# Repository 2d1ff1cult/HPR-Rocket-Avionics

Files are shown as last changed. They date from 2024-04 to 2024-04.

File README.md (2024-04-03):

# HPR Rocket Avionics
Code for data acquisition electronics on a Tripoli Level 1 High Power Rocket (HPR)

Model as of 4/2/2024:
As of 4/2/2024, this is the first iteration. Currently just collects data and ~~stores on SD card~~ displays to ground station serial monitor.
Uses nRF24L01+ 2.4GHz modules for radio communication.

Features the uses of remove before flight (RBF) tags connected to SPDT switches in a custom CAD assembly to actuate GPS and logging first, then the Arduino Nano.
handdrawn schematic

Why? GPS cold starts are a big issue; starting the GPS at least 15 minutes before the entire data logging circuit allows for satellite acquisition as you drive to rocket launch destination.

Sample data looks like this:
sampledata

Second iteration will be an upgrade to 900MHz with RYLR998 and data logging. Possibly even control loops for fin actuation.

Future goals involve creating an OSD visualization of the data (which are altitude, air pressure, speed, XYZ accel, and GPS) similar to SpaceX launches. This is what inspired this work


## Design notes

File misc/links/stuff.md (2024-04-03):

arduino
https://support.arduino.cc/hc/en-us/articles/4841602539164-Burn-the-bootloader-on-UNO-Mega-and-classic-Nano-using-another-Arduino

nrf24l01
https://lastminuteengineers.com/nrf24l01-arduino-wireless-communication/
https://forum.arduino.cc/t/simple-nrf24l01-2-4ghz-transceiver-demo/405123/2

gps
https://github.com/SlashDevin/NeoGPS/blob/master/examples/NMEASDlog/NMEASDlog.ino

lora
https://how2electronics.com/reyax-rylr890-lora-module-with-arduino/
https://www.thethingsnetwork.org/docs/lorawan/spreading-factors/
https://www.youtube.com/watch?v=dxYY097QNs0
https://www.youtube.com/watch?v=B580NvdXtjs

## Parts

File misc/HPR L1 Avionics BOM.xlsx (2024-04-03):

Quantity | Component | Dimensions | Links | Notes
2 | Microcontroller Unit (MCU): Arduino Nano | 45mm x 18mm | link (https://www.ebay.com/itm/364546971433?itmmeta=01HTH1EPV5RG68D9N0ZWATMX4W) | Need CH340 drivers
1 | Accelerometer + Gyroscope + Compass: MPU9250 | 15mm x 25mm | link (https://www.ebay.com/itm/404781821679?itmmeta=01HTH1E781Y8EGJHDQG15KYYSF)
2 | 900MHz Long Range Radio (LoRa): RYLR998 | 32mm x 14mm | link (https://www.amazon.com/gp/product/B099RM1XMG/ref=ppx_yo_dt_b_search_asin_title?ie=UTF8&psc=1)
1 | Altimeter: BMP388 | 169mm x 66mm | link (https://www.amazon.com/gp/product/B09FG4NXFJ/ref=ppx_yo_dt_b_search_asin_title?ie=UTF8&psc=1)
1 | GPS: NEO-6M | 90mm x 55mm | link (https://www.amazon.com/gp/product/B0CPX7B1KW/ref=ppx_yo_dt_b_search_asin_title?ie=UTF8&psc=1)
1 | SD Reader: HW125 SD Reader Breakout Board | 102mm x 79mm | link (https://www.amazon.com/gp/product/B07BJ2P6X6/ref=ppx_yo_dt_b_search_asin_title?ie=UTF8&psc=1)
2 | buck regulators | 20mm x 11mm | link (https://www.amazon.com/gp/product/B08R6337QY/ref=ppx_yo_dt_b_search_asin_title?ie=UTF8&psc=1)
2 | SPDT switches | 20mm x 10mm | link (https://www.amazon.com/gp/product/B07MW2RPJY/ref=ppx_yo_dt_b_search_asin_title?ie=UTF8&psc=1) | for use with RBF switches

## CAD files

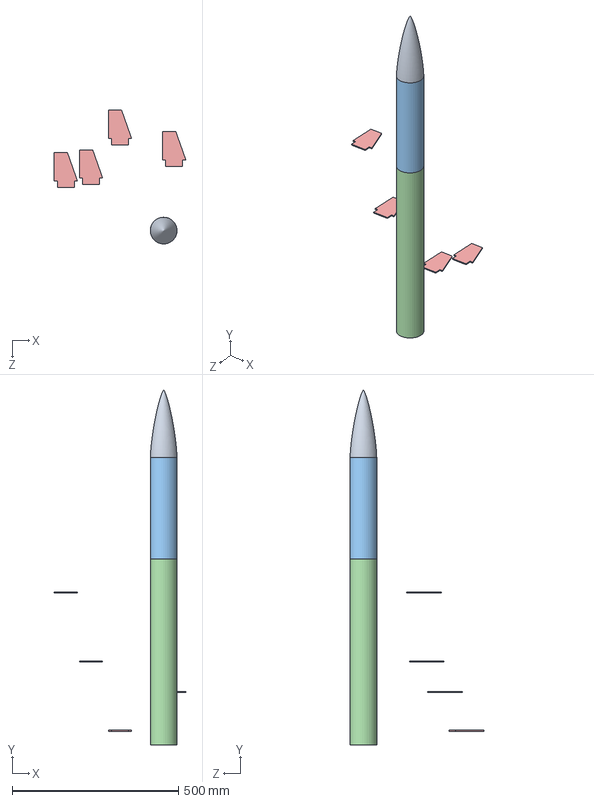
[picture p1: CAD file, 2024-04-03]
cad/Jerome_Rocket.SLDASM
395.8 x 1066.8 x 402.4 mm
Jerome Bulkhead
Jerome Fins x 4
Jerome Lower Body Tube
Jerome Top Body Tube
Jerome Tube Coupler
Jerome_Nose_Cone

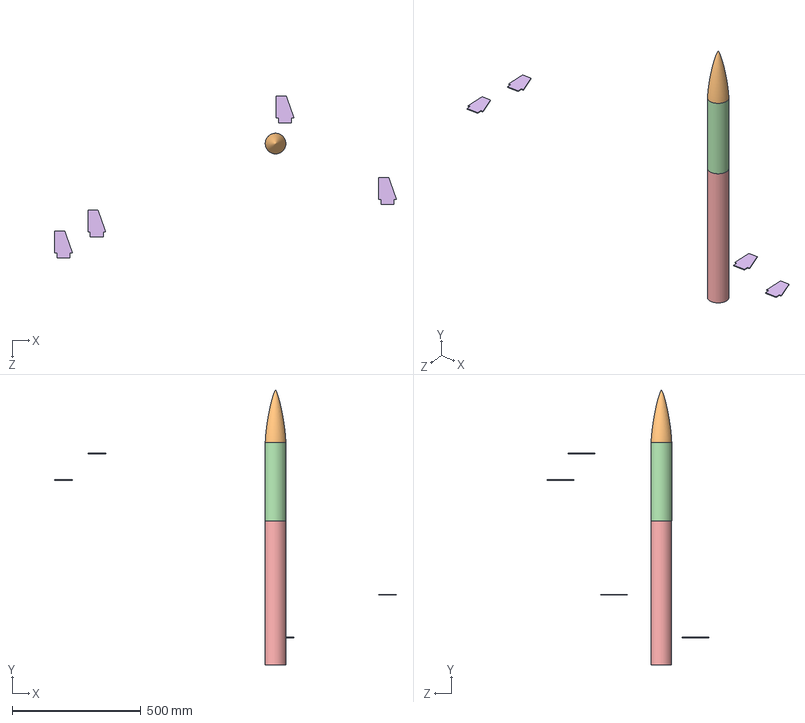
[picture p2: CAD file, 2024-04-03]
cad/Jerome_Rocket rev2.SLDASM
1326.9 x 1066.8 x 627.6 mm
Jerome Bulkhead
Jerome Centering Ring x 3
Jerome Fins x 4
Jerome Lower Body Tube
Jerome Top Body Tube
Jerome Tube Coupler
Jerome_Nose_Cone
Jerome Inner Tube

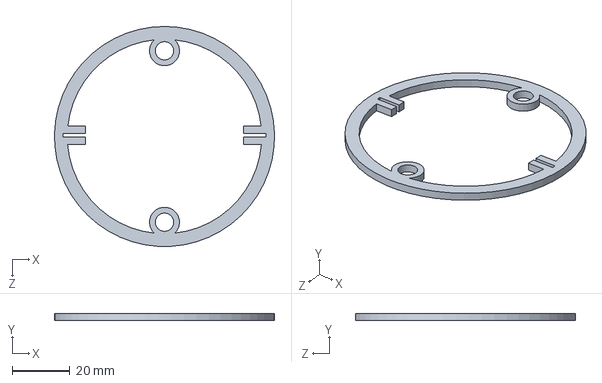
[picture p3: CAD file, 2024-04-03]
cad/PCB_coupler_crosssection.SLDPRT
76.2 x 2.54 x 76.2 mm

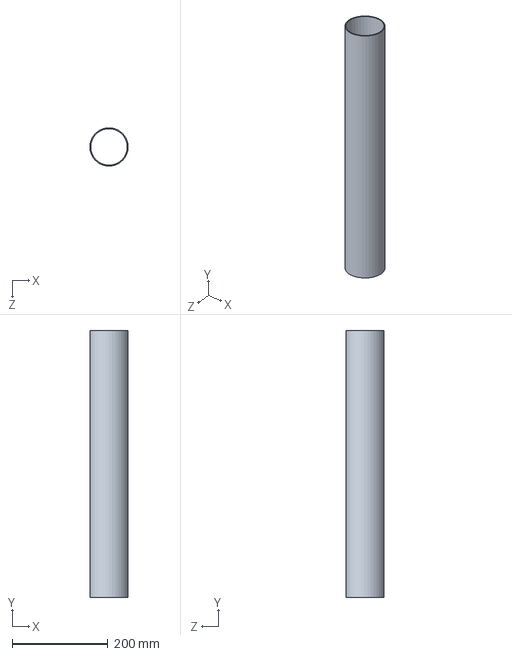
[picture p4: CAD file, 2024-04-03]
cad/Jerome Lower Body Tube.SLDPRT
80.2 x 558.8 x 80.2 mm

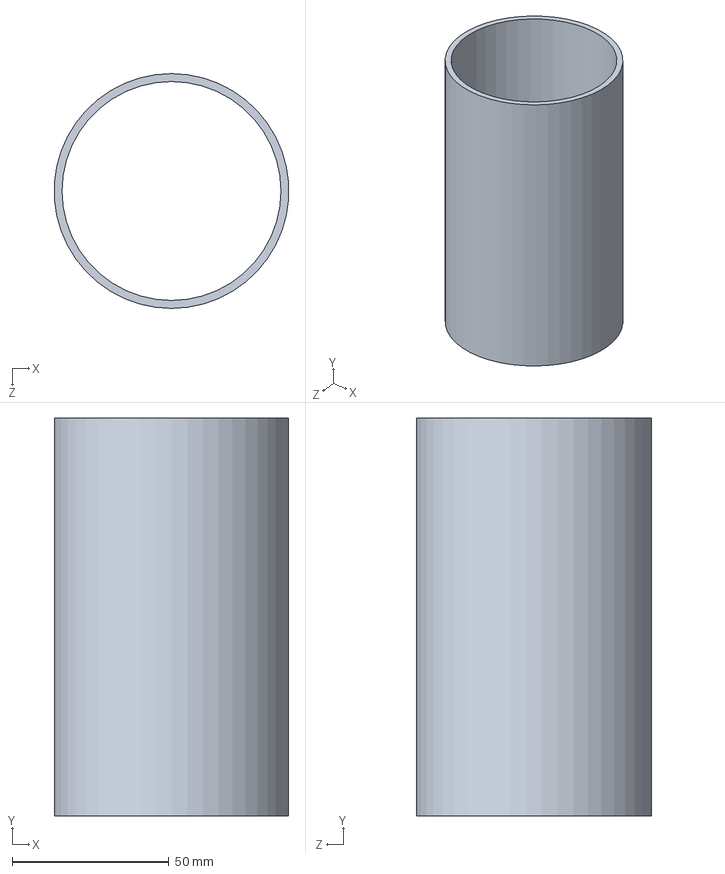
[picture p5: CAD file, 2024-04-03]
cad/Jerome Tube Coupler.SLDPRT
74.8 x 127.0 x 74.9 mm

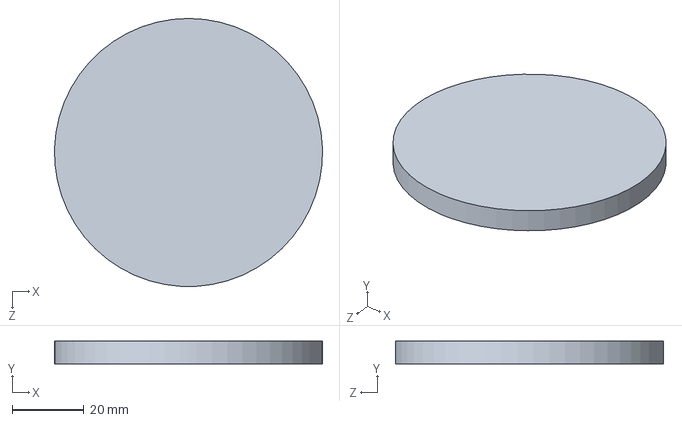
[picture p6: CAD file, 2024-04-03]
cad/Jerome Bulkhead.SLDPRT
74.9 x 6.35 x 74.9 mm

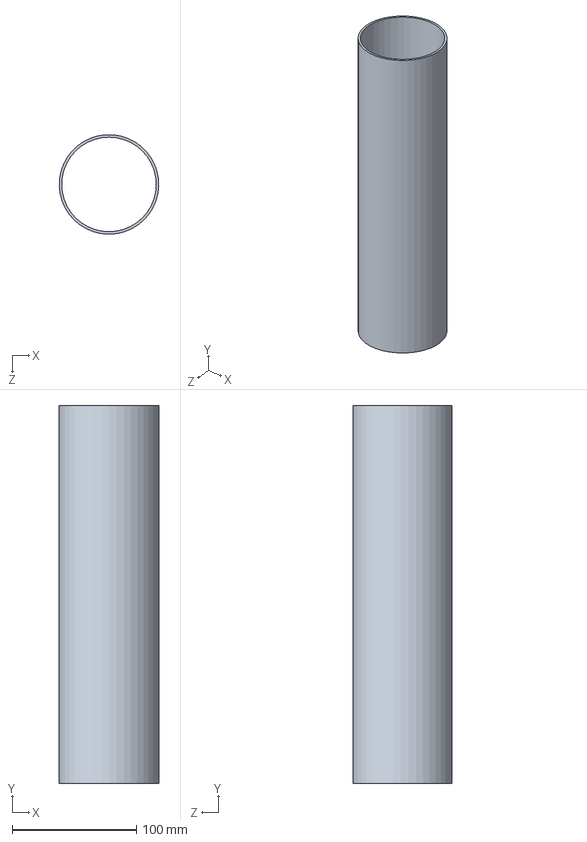
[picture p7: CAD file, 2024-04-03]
cad/Jerome Top Body Tube.SLDPRT
80.3 x 304.8 x 80.2 mm

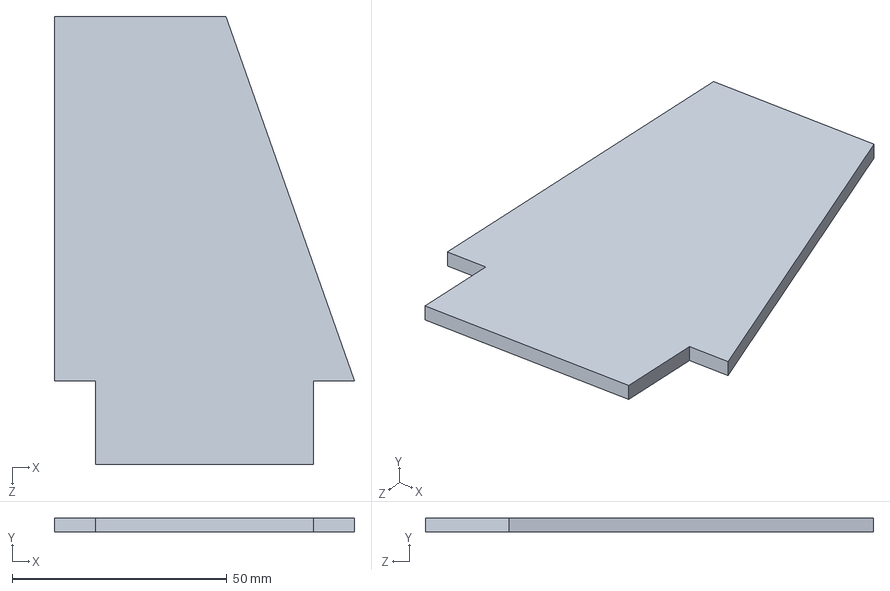
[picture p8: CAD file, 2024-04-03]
cad/Jerome Fins.SLDPRT
70.0 x 3.17 x 104.4 mm

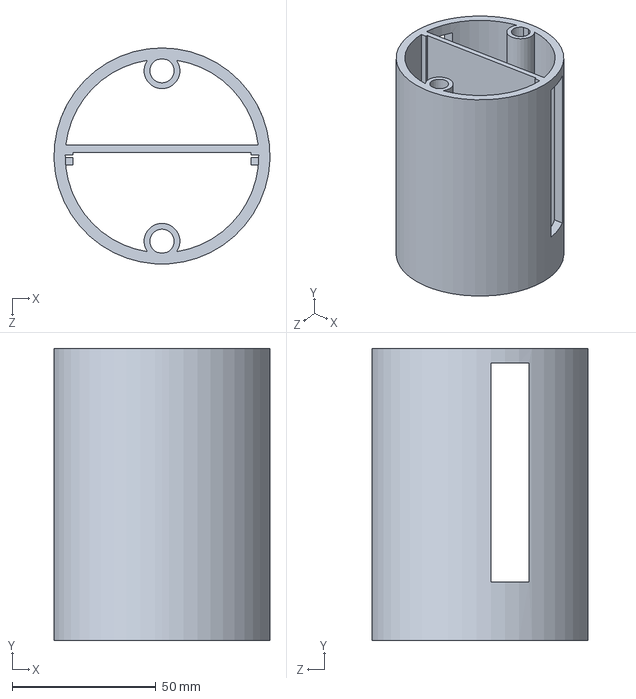
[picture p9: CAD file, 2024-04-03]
cad/PCB_coupler.SLDPRT
75.1 x 101.6 x 75.2 mm

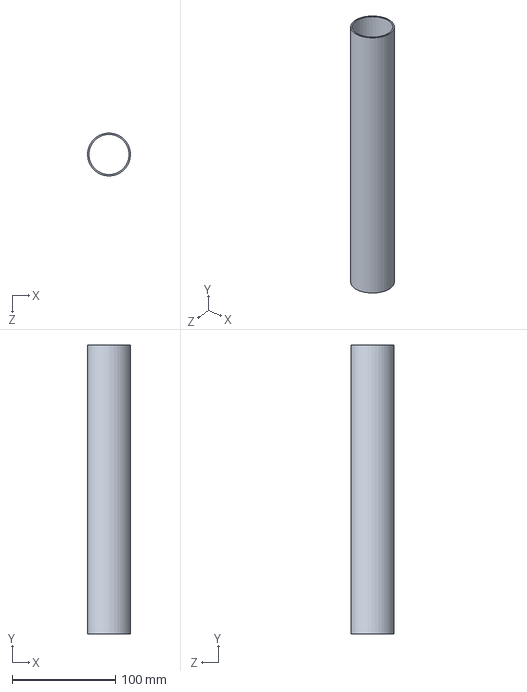
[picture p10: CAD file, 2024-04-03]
cad/Jerome Inner Tube.SLDPRT
41.5 x 279.4 x 41.5 mm

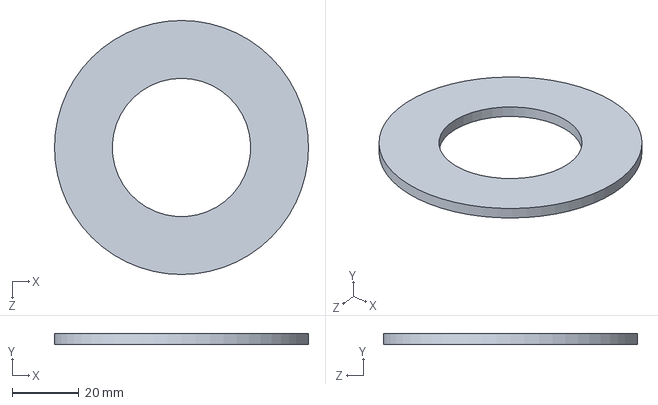
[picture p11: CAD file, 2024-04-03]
cad/Jerome Centering Ring.SLDPRT
76.2 x 3.17 x 76.2 mm

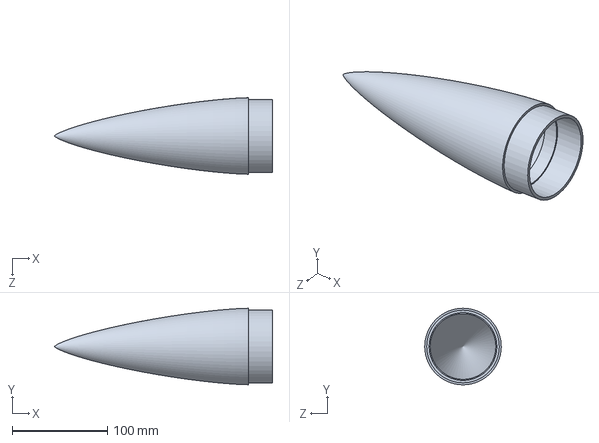
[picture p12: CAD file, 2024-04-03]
cad/Jerome_Nose_Cone.SLDPRT
228.6 x 80.3 x 80.3 mm

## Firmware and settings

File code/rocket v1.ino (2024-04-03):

/*
LAKAS-1
a Tripoli Level 1 (L1) High-Power Rocket (HPR)

Code description:
Uses the following sensors:
- Altitude:
  - BMP388 altimeter (spec. barometric pressure sensor)
- Orientation, velocity, and angular velocities:
  - MPU6050 6DOF MEMS accelerometer + gyroscope
- Telemetry:
  - nRF24L01 + PA + LNA (power amplifier + low noise amplifier)
    - Operates at 250 KBPS
- Positioning
  - uBlox NEO-6M
    - really cool GPS device
- Logging
  - HW-125 SD breakout board
    - 5V to 3.3V LDO for easy usage
    - don't forget to format SD card to FAT32!

Rationale:
Get basic flight data from rocket during flight and send in real-time to ground station (aka my laptop)

Wiring:
BMP388    Nano
VIN       5V
GND       GND
SCK       A5
SDI       A4

MPU6050   Nano
VCC       5V
GND       GND
SCK       A5
SCL       A4

nRF24L01  Nano
VCC       5V (note: using adapter)
GND       GND
CE        9
CSN       10
SCK       13
MOSI      11
MISO      12

NEO-6M    Nano
VCC       external power
RX        4
TX        3
GND       GND

HW-125    Nano
VCC       5V
GND       GND
CS        5
MOSI      11
MISO      12
CLK       13

v3 Changelog:
03/19/2024 - launch was scrapped, moved to 4/20/2024
03/17/2024 - finally receiving GPS coords in this program; was missing checking if SoftwareSerial was available
03/19/2024 - verifed receipt on RX of GPS signals

v2 Changelog:
03/16/2024 - not working with GPS even though GPS examples working
03/16/2024 - updated receiver code, confirmed receiving
03/14/2024 - sd card causes nano to not work, still fixing

*/

#include <Wire.h> // I2C
#include <SPI.h> //SPI
#include <SoftwareSerial.h> // serial for GPS
#include <TinyGPS.h>  // TinyGPS for post processing

// sd
#include <SD.h>

// altimeter
#include <Adafruit_BMP3XX.h>
#include <Adafruit_Sensor.h>
#include "Adafruit_BMP3XX.h"
#include <bmp3.h>
#include <bmp3_defs.h>
#define SEALEVELPRESSURE_HPA (1013.25)

// accelgyro
#include "I2Cdev.h"
#include <MPU6050.h> // accel + gyro

// nRF24L01 libs
#include <RF24.h>
#include <RF24_config.h>
#include <nRF24L01.h>
#include <printf.h>

#define CE_PIN   9
#define CSN_PIN 10

// sensor definitions
Adafruit_BMP3XX bmp; // defining a sensor called bmp
MPU6050 mpu; // defining a sensor called mpu
SoftwareSerial ss(4,3); // defining a SoftwareSerial device called ss
TinyGPS gps;
RF24 radio(CE_PIN, CSN_PIN); // Create a Radio

float getgps(TinyGPS &gps);


const byte address[5] = {'U','r','m','o','m'};

// timekeeping and misc. vars
float currenttime; //used to be long but this caused timing issues where a decimal point was omitted
unsigned long lasttime;
int16_t ax, ay, az, gx, gy, gz;
int16_t gyro_angle_x_l, gyro_angle_y_l;
int16_t angle_x_l, angle_y_l;
int16_t ax_offset, ay_offset, az_offset, gx_offset, gy_offset, gz_offset;
const float KMPH = 3.6;
const float ALPHA = 0.96;
const float CONST_16G = 2048;
const float CONST_2000 = 16.4;
const float CONST_G = 9.81;
const float RADIANS_TO_DEGREES = 180 / 3.14159;

unsigned long age;
float gpslat, gpslon, gpsalt, gpsspd;

const int sdcs = 5;

void setup(){
  // debugging
  // TODO: remove
  Serial.begin(115200);
  ss.begin(9600);    // gps

  // Set up oversampling and filter initialization
  bmp.begin_I2C();
  bmp.setTemperatureOversampling(BMP3_OVERSAMPLING_8X);
  bmp.setPressureOversampling(BMP3_OVERSAMPLING_4X);
  bmp.setIIRFilterCoeff(BMP3_IIR_FILTER_COEFF_3);
  bmp.setOutputDataRate(BMP3_ODR_50_HZ);

  Wire.begin();   // gyro; per MPU6050 lib, this joins i2c bus
  mpu.initialize();
  calibratesensors();  // initialize sensor hardware

  radio.begin();    // radio initialize
  radio.setDataRate(RF24_250KBPS);
  radio.setPALevel(RF24_PA_MAX);
  radio.setRetries(10,10);
  radio.openWritingPipe(address);
}
void loop(){
  bool sending;
  currenttime = millis(); // time from start (milliseconds)
  float alt = int(bmp.readAltitude(SEALEVELPRESSURE_HPA));
  float pressure = bmp.pressure / 100.0;
  //getgps(gps); // lat lon alt spd
  bool sent; //checks if last packet was sent
  while(ss.available()){
    char c = ss.read();
      if(gps.encode(c)){
        gps.f_get_position(&gpslat, &gpslon,&age);
        gpsalt = gps.f_altitude();
        gpsspd = gps.f_speed_kmph();
      }
  }
  float radiodata[] = {
                        currenttime, // milliseconds
                        alt, // m
                        //pressure, //hpa
                        velocity(currenttime), // kmh
                        gpslat, gpslon,
                        (ax - ax_offset) / CONST_16G,
                        (ay - ay_offset) / CONST_16G,
                        (az - az_offset) / CONST_16G,
                      };
    sending = radio.write(&radiodata, sizeof(radiodata)); // simultaneously define if message was sent and sending message
    if(sending){
      Serial.print("Sent!\t");
    } else{
      Serial.print("Fail!\t");
    }
    sent = sending; // storing current loop radio status
    //TODO: delete this before flight
    for(int i = 0; i < 3; i++)
    {
      Serial.print(radiodata[i]);
      Serial.print('\t');
    }
    for(int i = 0; i<5;i++){
      Serial.print(radiodata[i+3],6);
      Serial.print('\t');
    }
    Serial.print(sizeof(radiodata));
    Serial.println();

  // end todo
  set_last_time(currenttime);
}

//funcs
void calibratesensors() {
  Serial.println("Setting offsets");
  int                   num_readings = 100;
  float                 x_accel = 0;
  float                 y_accel = 0;
  float                 z_accel = 0;
  float                 x_gyro = 0;
  float                 y_gyro = 0;
  float                 z_gyro = 0;

  // Discard the first set of values read from the IMU
  mpu.getMotion6(&ax, &ay, &az, &gx, &gy, &gz);

  // Read and average the raw values from the IMU
  for (int i = 0; i < num_readings; i++) {
    mpu.getMotion6(&ax, &ay, &az, &gx, &gy, &gz);

    x_accel += ax;
    y_accel += ay;
    z_accel += az;
    x_gyro += gx;
    y_gyro += gy;
    z_gyro += gz;
    delay(10);
  }
  x_accel /= num_readings;
  y_accel /= num_readings;
  z_accel /= num_readings;
  x_gyro /= num_readings;
  y_gyro /= num_readings;
  z_gyro /= num_readings;

  // Store the raw calibration values globally
  ax_offset = x_accel;
  ay_offset = y_accel;
  az_offset = z_accel;
  gx_offset = x_gyro;
  gy_offset = y_gyro;
  gz_offset = z_gyro;

  Serial.print("Offsets: ");
  Serial.print(ax_offset);
  Serial.print(", ");
  Serial.print(ay_offset);
  Serial.print(", ");
  Serial.print(az_offset);
  Serial.print(", ");
  Serial.print(gx_offset);
  Serial.print(", ");
  Serial.print(gy_offset);
  Serial.print(", ");
  Serial.println(gz_offset);
  
  Serial.println("Finishing Calibration");
}

float getgps(TinyGPS &gps){
  char c = ss.read();
  gps.encode(c);
  gps.f_get_position(&gpslat, &gpslon,&age); //get floating point lat/long
  gpsalt = gps.f_altitude();
  gpsspd = gps.f_speed_kmph();
  Serial.print(gpslat == TinyGPS::GPS_INVALID_F_ANGLE ? 0.0 : gpslat, 6);
  //return gpslat, gpslon, gpsalt, gpsspd;
}

// mathy stuff
float velocity(float t_now){
  float dt = get_dt(t_now);
  mpu.getMotion6(&ax, &ay, &az, &gx, &gy, &gz);

  float ax_p = (ax - ax_offset) / CONST_16G;
  float ay_p = (ay - ay_offset) / CONST_16G;
  float az_p = (az - az_offset) / CONST_16G;

  float accel_angle_y = atan(-1 * ax_p / sqrt(pow(ay_p, 2) + pow(az_p, 2))) * RADIANS_TO_DEGREES;
  float accel_angle_x = atan(ay_p / sqrt(pow(ax_p, 2) + pow(az_p, 2))) * RADIANS_TO_DEGREES;

  float gx_p = (gx - gx_offset) / CONST_2000;
  float gy_p = (gy - gy_offset) / CONST_2000;
  float gz_p = (gz - gz_offset) / CONST_2000;

  float gyro_angle_x = gx_p * dt + get_last_angle_x();
  float gyro_angle_y = gy_p * dt + get_last_angle_y();

  float angle_x = ALPHA * gyro_angle_x + (1.0 - ALPHA) * accel_angle_x;
  float angle_y = ALPHA * gyro_angle_y + (1.0 - ALPHA) * accel_angle_y;

  float vel_x = (ax_p * (dt/1000) * CONST_G);
  float vel_y = (ay_p * (dt/1000) * CONST_G);
  float vel_z = (az_p * (dt/1000) * CONST_G);
  float vel = sqrt(pow(vel_x, 2) + pow(vel_y, 2) + pow(vel_z, 2)) * KMPH;
  return vel;//, angle_x, angle_y;
  // sd.write(ax, ay, az, gx, gy, gz) or some function to write raw
}


inline unsigned long get_last_time() {
  return lasttime;
}

inline void set_last_time(unsigned long _time) {
  lasttime = _time;
}

inline float get_dt(unsigned long t_now) {
  return (t_now - get_last_time());
}
inline int16_t get_last_gyro_angle_x() {
  return gyro_angle_x_l;
}

inline void set_last_gyro_angle_x(int16_t _gyro_angle_x) {
  gyro_angle_x_l = _gyro_angle_x;
}

inline int16_t get_last_gyro_angle_y() {
  return gyro_angle_y_l;
}

inline void set_last_gyro_angle_y(int16_t _gyro_angle_y) {
  gyro_angle_y_l = _gyro_angle_y;
}

inline int16_t get_last_angle_x() {
  return angle_x_l;
}

inline void set_last_angle_x(int16_t _ang_x) {
  angle_x_l = _ang_x;
}

inline int16_t get_last_angle_y() {
  return angle_y_l;
}

inline void set_last_angle_y(int16_t _ang_y) {
  angle_y_l = _ang_y;
}


// TODO:check this shit
// write to sd
// can this write in csv?
void sdwrite(){

}

// notes
// some text
/*
from adafruit:
http://www.adafruit.com/datasheets/BST-BMP180-DS000-09.pdf
this is the formula used to compute altitude
  float atmospheric = readPressure() / 100.0F;
  return 44330.0 * (1.0 - pow(atmospheric / seaLevel, 0.1903));
*/

/*
Bibliography (spec. for modified code):
https://github.com/arashmarzi/speedometer/blob/master/speedometer.ino
https://forum.arduino.cc/t/simple-nrf24l01-2-4ghz-transceiver-demo/405123/2
https://aprs.gids.nl/nmea/
https://randomnerdtutorials.com/guide-to-neo-6m-gps-module-with-arduino/
https://lastminuteengineers.com/neo6m-gps-arduino-tutorial/
https://learnarduinonow.com/2014/02/22/arduino-ublox-neo-6m-gps.html
https://www.youtube.com/watch?v=IGusY74xMR8
*/

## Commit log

2024-04-03 Rename Ground_Station_for_LAKAS-L1-v2.ino to Ground Station.ino
2024-04-03 Rename Ground Station.ino to code/Ground Station.ino
2024-04-03 Create cad
2024-04-03 Rename Jerome Bulkhead.SLDPRT to cad/Jerome Bulkhead.SLDPRT
    [Jerome Bulkhead.SLDPRT]
2024-04-03 Rename code/Ground Station.ino to code/v1/Ground Station.ino
2024-04-03 Rename code/v1/Ground Station.ino to code/Ground Station.ino
2024-04-03 Rename Ground_Station_for_LAKAS-L1-v2.ino to code/ground station v1
2024-04-03 Rename HPR L1 Avionics BOM.xlsx to misc/HPR L1 Avionics BOM.xlsx
    [HPR L1 Avionics BOM.xlsx]
